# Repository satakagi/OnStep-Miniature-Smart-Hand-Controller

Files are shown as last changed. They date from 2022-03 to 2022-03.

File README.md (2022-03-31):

# OnStep-Miniature-Smart-Hand-Controller

## About
This is a much smaller design of the [Smart Hand Controller (SHC)](https://onstep.groups.io/g/main/wiki/7152) for [OnStep](https://onstep.groups.io/g/main)*1.
It is based on the [OnStep ESP32 Smart Hand Controller](https://baheyeldin.com/astronomy/onstep-esp32-smart-hand-controller-shc.html) circuit.

Therefore, the firmware is exactly the same as the ESP32 SHC, see the section Installing the Platform - For the ESP32 SHC on [The Smart Hand Controller (SHC)](https://onstep.groups.io/g/main/wiki/7152) page.

*1: OnStep is an open source GoTo motor drive for telescope mounts

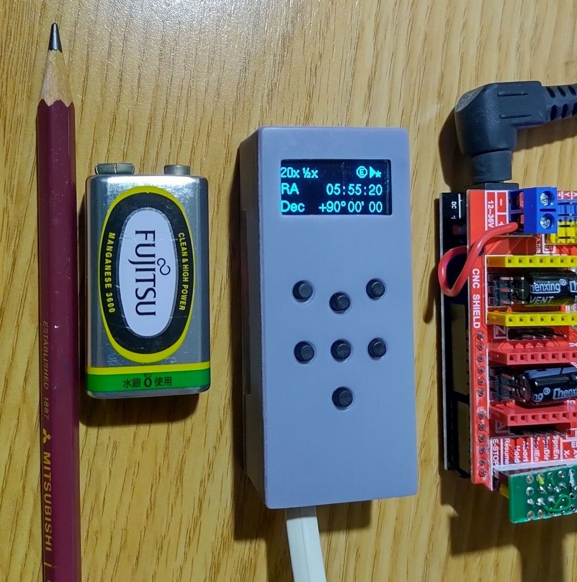
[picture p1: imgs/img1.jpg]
mini SHC working image


## Parts List

* [DOIT ESP32 DEVKIT V1](https://www.amazon.com/s?k=DOIT+ESP32+DEVKIT+V1)
  * Note: Unlike the original ESP32 SHC, this design uses the DOIT ESP32 DEVKIT V1 with 30 pins.
* PCB ( refer to [kicad](kicad/) directory )
* [0.96" SSD1306 OLED Module](https://www.amazon.com/s?k=0.96+ssd1306+oled)
  * Note: Stick tape on the back side for insulation.
* Modular Jack 6P6C x 2
  * The plastic pins for fixing the jacks should be cut out.
* 7 Resistor Network (2K ohm)
* 4 Resistor Network (2K ohm)
* 2.54mm Header Pins 15pin F x 2, 4pin M, 2pin M 
* Momentary Tact Button Switches 0.2" x 0.24" x 7
  * Buttons would need to be at least 0.24" long.
* Case ( refer to [miniSHCcase.stl](miniSHCcase.stl) )
  * The example on this page were produced using the MSLA LCD 3d printer.

## Photos of the interior structure
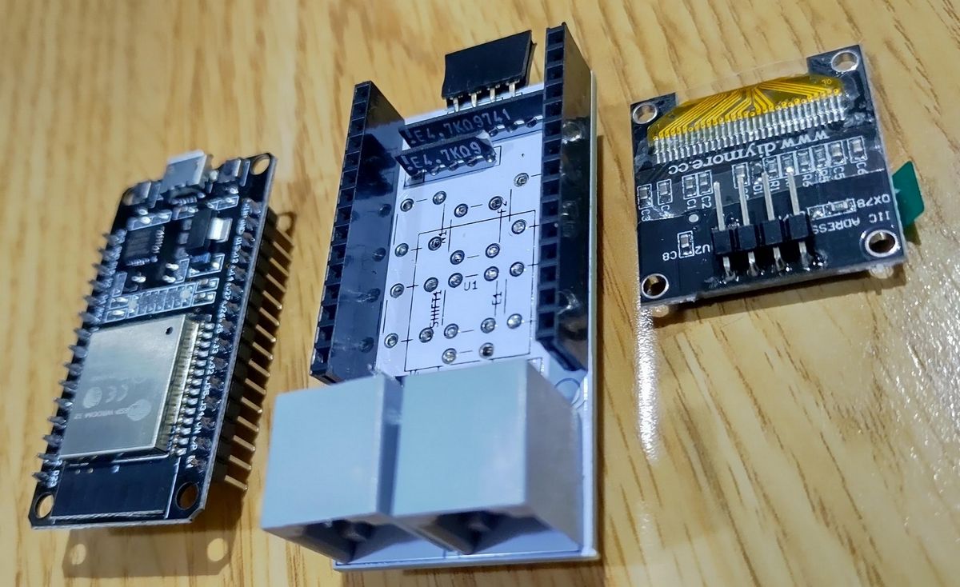
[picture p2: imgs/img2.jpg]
Three modules make up the controller

Tape is attached to the back of the OLED module for insulation.
|  - |  -  |
| ---- | ---- |
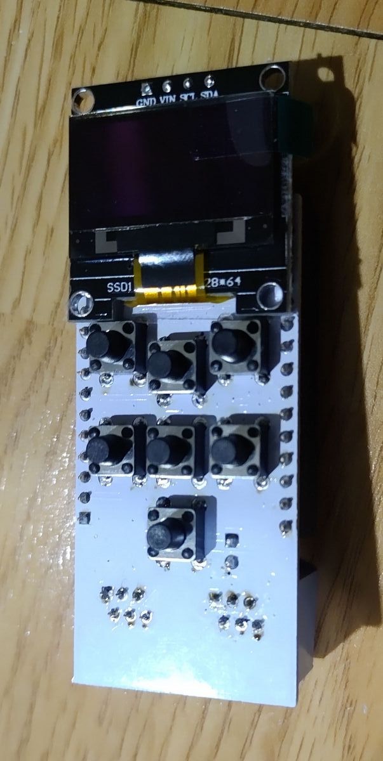
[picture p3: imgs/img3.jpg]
PCB
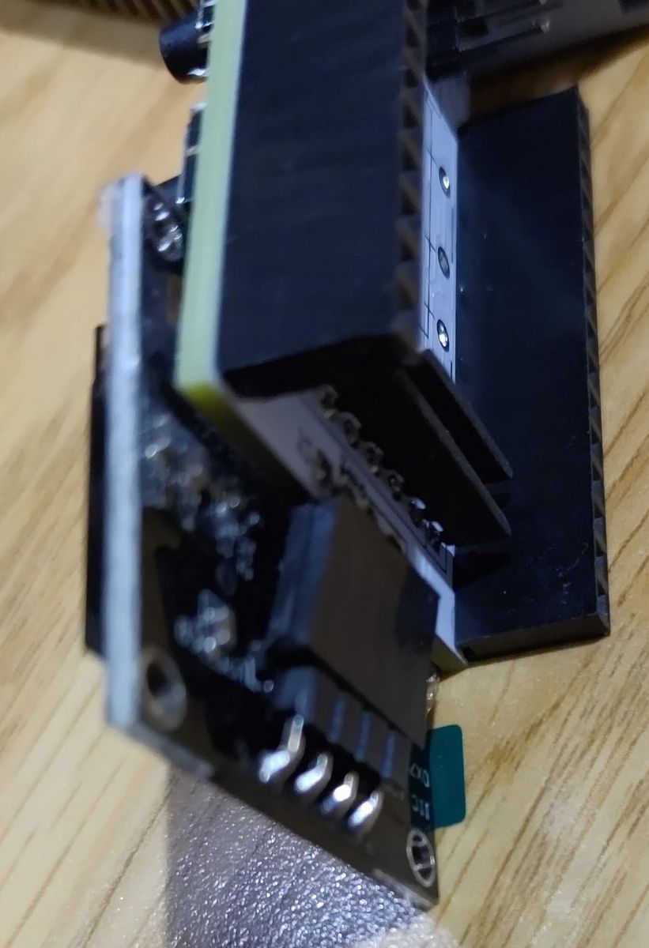
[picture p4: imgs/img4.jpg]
Connection with OLED
|    |    |
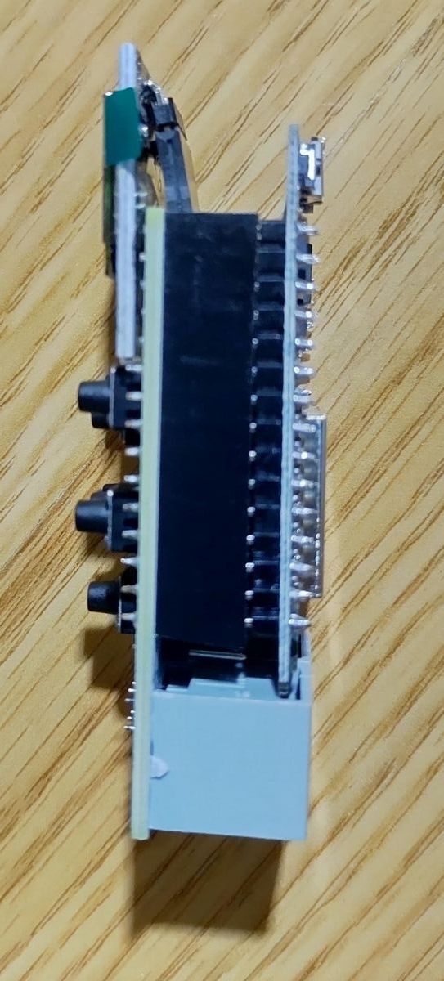
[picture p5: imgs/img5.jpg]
Side view
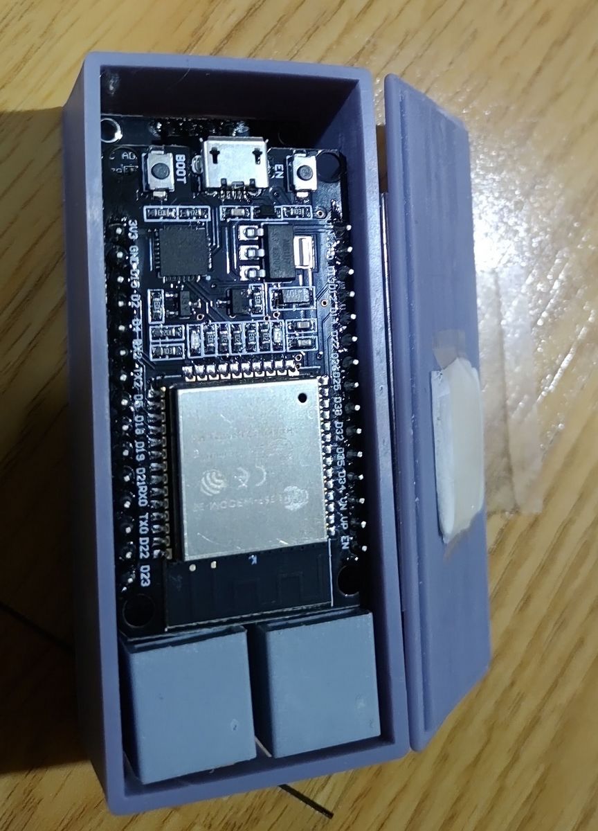
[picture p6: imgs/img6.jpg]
Backside view and installation in a case
|  <br>To avoid interference with the OLED, the leads protruding from the through-holes are trimmed.  |  <br>Attach a pad to the lid to hold the board in place and close the lid. (In this picture, the lid is fastened with tape.) |

## License
This is licensed under the [TAPR Open Hardware License](https://tapr.org/the-tapr-open-hardware-license/), one of the well-known open-source hardware licenses.

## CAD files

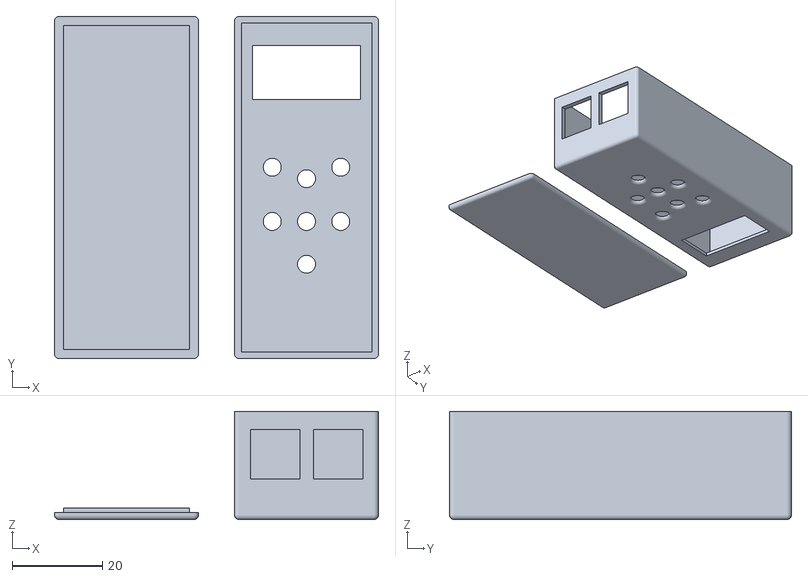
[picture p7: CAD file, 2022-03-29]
miniSHCcase.stl
72.0 x 76.0 x 24.0

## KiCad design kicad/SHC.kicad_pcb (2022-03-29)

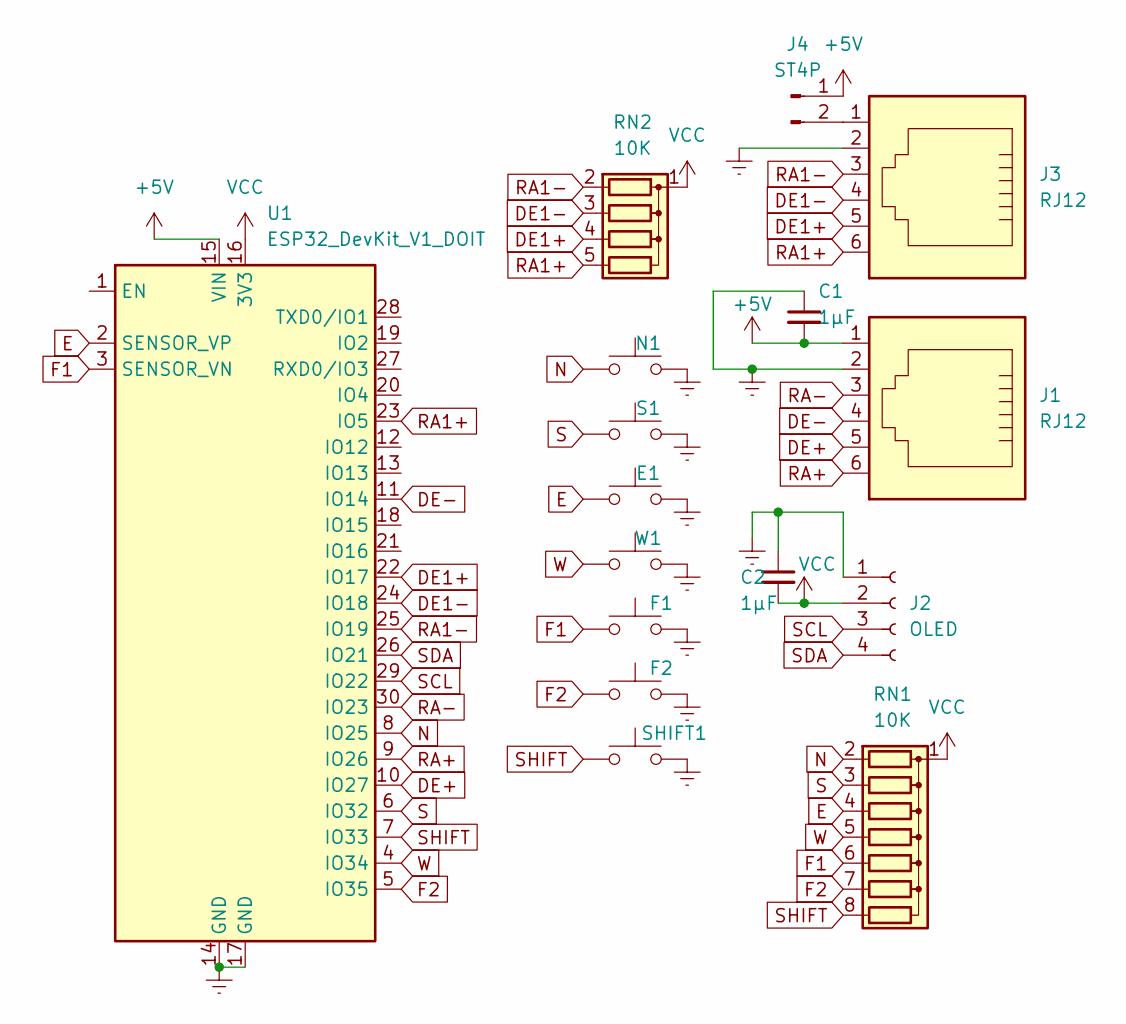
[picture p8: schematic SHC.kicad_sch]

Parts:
C1, C2: 1μF; C_Disc_D5.0mm_W2.5mm_P2.50mm
E1: SW_Push; SW_PUSH_6mm_H8mm
F1, F2: SW_Push; SW_PUSH_6mm_H8mm
J1, J3: RJ12; RJ25_Wayconn_MJEA-660X1_Horizontal_NoSupport
J2: OLED; PinHeader_1x04_P2.54mm_Vertical
J4: ST4P; PinHeader_1x02_P2.54mm_Vertical
N1: SW_Push; SW_PUSH_6mm_H8mm
RN1: 10K; R_Array_SIP8
RN2: 10K; R_Array_SIP5
S1: SW_Push; SW_PUSH_6mm_H8mm
SHIFT1: SW_Push; SW_PUSH_6mm_H8mm
U1: ESP32_DevKit_V1_DOIT; esp32_devkit_v1_doit
W1: SW_Push; SW_PUSH_6mm_H8mm

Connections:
+5V: C1.2, J1.1, J4.1, U1.15 (VIN)
DE1+: J3.5, RN2.4 (R3), U1.22 (IO17)
DE1-: J3.4, RN2.3 (R2), U1.24 (IO18)
DE+: J1.5, U1.10 (IO27)
DE-: J1.4, U1.11 (IO14)
E: E1.1, RN1.4 (R3), U1.2 (SENSOR_VP)
Earth: C1.1, C2.1, E1.2, F1.2, F2.2, J1.2, J2.1, J3.2, N1.2, S1.2, SHIFT1.2, U1.14 (GND), U1.17 (GND), W1.2; also elsewhere on the board
F1: F1.1, RN1.6 (R5), U1.3 (SENSOR_VN)
F2: F2.1, RN1.7 (R6), U1.5 (IO35)
N: N1.1, RN1.2 (R1), U1.8 (IO25)
unnamed: J3.1, J4.2
RA1+: J3.6, RN2.5 (R4), U1.23 (IO5)
RA1-: J3.3, RN2.2 (R1), U1.25 (IO19)
RA+: J1.6, U1.9 (IO26)
RA-: J1.3, U1.30 (IO23)
S: RN1.3 (R2), S1.1, U1.6 (IO32)
SCL: J2.3, U1.29 (IO22); also elsewhere on the board
SDA: J2.4, U1.26 (IO21); also elsewhere on the board
SHIFT: RN1.8 (R7), SHIFT1.1, U1.7 (IO33)
VCC: C2.2, J2.2, RN1.1 (common), RN2.1 (common), U1.16 (3V3); also elsewhere on the board
W: RN1.5 (R4), U1.4 (IO34), W1.1

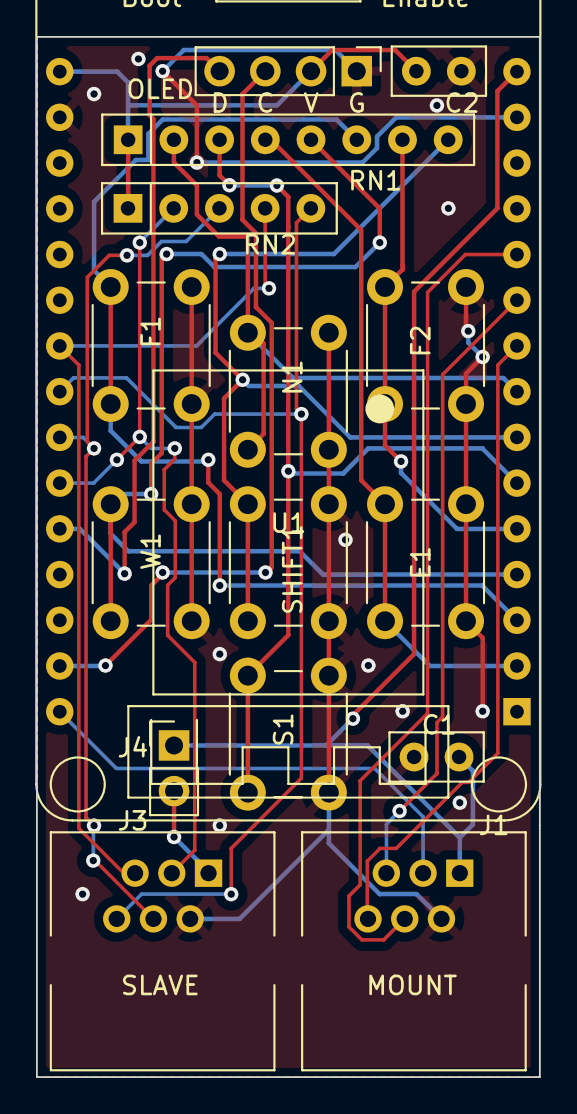
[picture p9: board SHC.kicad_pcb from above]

Board: 2 copper layers, 27.9 x 57.8 mm, 16 parts (0 on the bottom side), 21 nets.

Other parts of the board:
OLED: OLED; PinHeader_1x04_P2.54mm_Vertical

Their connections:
Earth: OLED.1; also elsewhere on the board
SCL: OLED.3; also elsewhere on the board
SDA: OLED.4; also elsewhere on the board
VCC: OLED.2; also elsewhere on the board
